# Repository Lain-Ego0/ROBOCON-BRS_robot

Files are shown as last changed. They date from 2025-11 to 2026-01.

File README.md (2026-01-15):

# ROBOCON-BRS_robot/黑岩射手
ROBOCON is a top-tier robotics competition that places high demands on mechanical reliability, electronic control stability, and visual accuracy.

ROBOCON作为机器人领域的顶尖赛事，对机械可靠性、电控稳定性、视觉准确性提出了较高的要求。

In the 2025 season, I was responsible for the full-stack R&D of the quadruped robot team, covering mechanical modeling, motion control, and autonomous navigation. Utilizing a carbon tube assembly mechanism similar to plant protection drones, force control algorithms, and 3D LiDAR mapping & navigation technology, our team achieved 30th place in the Speed Race, 31st in the Obstacle Race, and 34th in the Cross-Country Race at the 2025 ROBOCON (Jiangyin) among over 180 participating teams, winning Second Prize nationally in all three categories.

在2025赛季我基本完整负责了足式机器人一队从机械建模、运动控制到自主导航的全栈研发，采用类植保无人机碳管装配工艺机构+力控制算法+3D雷达建图导航技术，取得2025年ROBOCON（江阴）足式机器人竞速赛全国30名、障碍赛全国31名、越野赛全国34名（全国赛参赛队伍180余支）共三项国二的良好成绩。

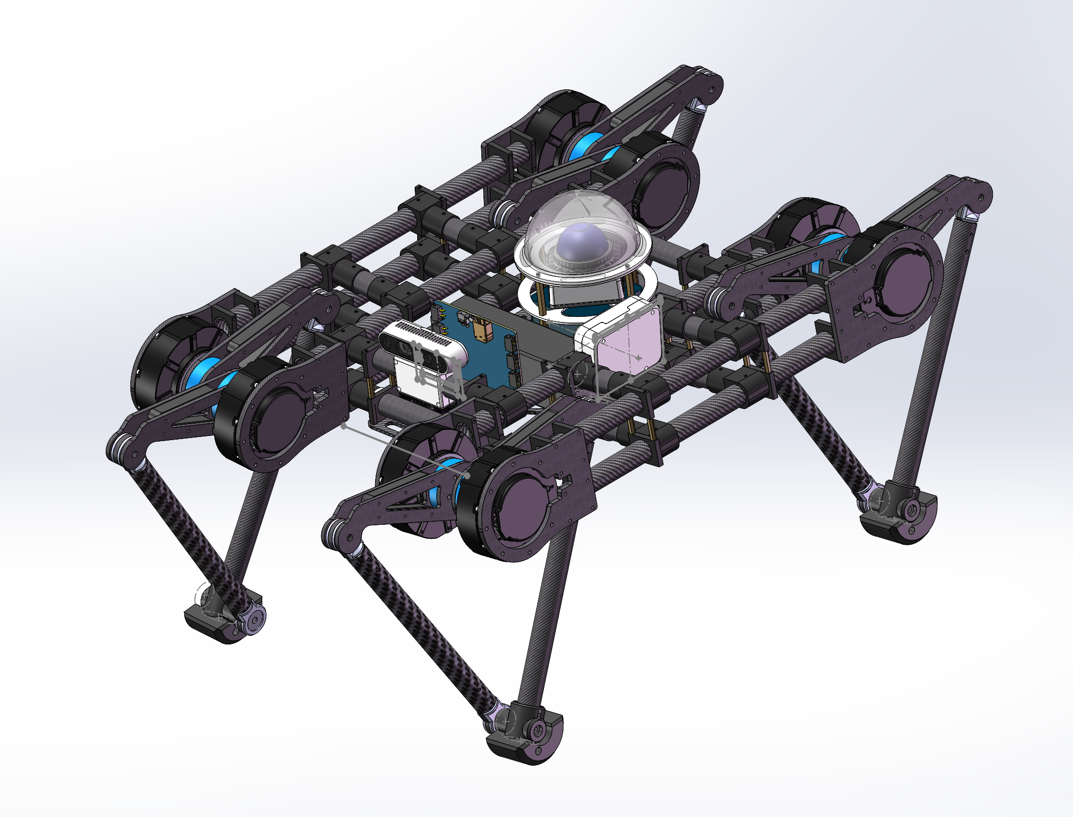
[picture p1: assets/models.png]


Post-calculation Visualization of Trajectory Demonstration and Inverse Kinematics Solution Demonstration in MATLAB

MATLAB计算后可视化的轨迹演示以及其逆解算演示

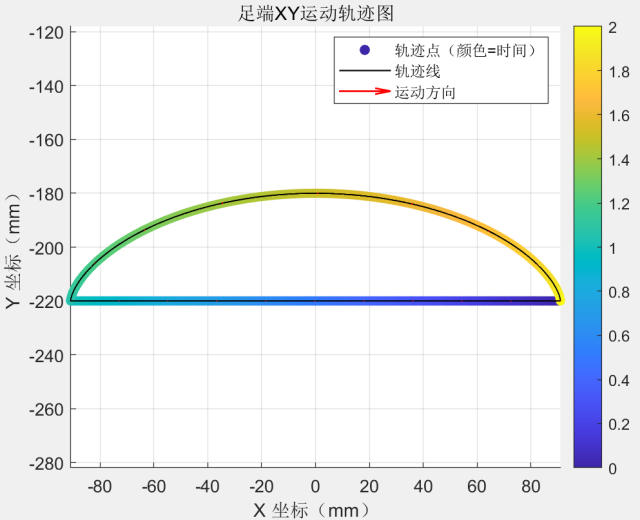
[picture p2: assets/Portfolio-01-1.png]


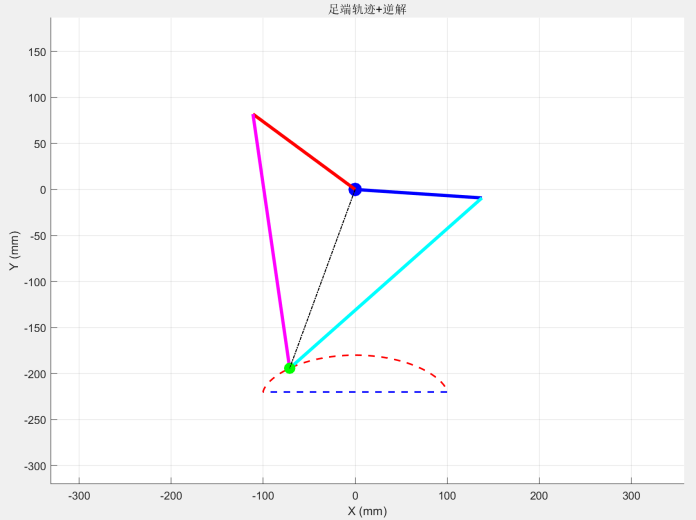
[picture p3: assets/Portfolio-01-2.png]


The system architecture diagram is shown in the figure.

系统架构图如图所示

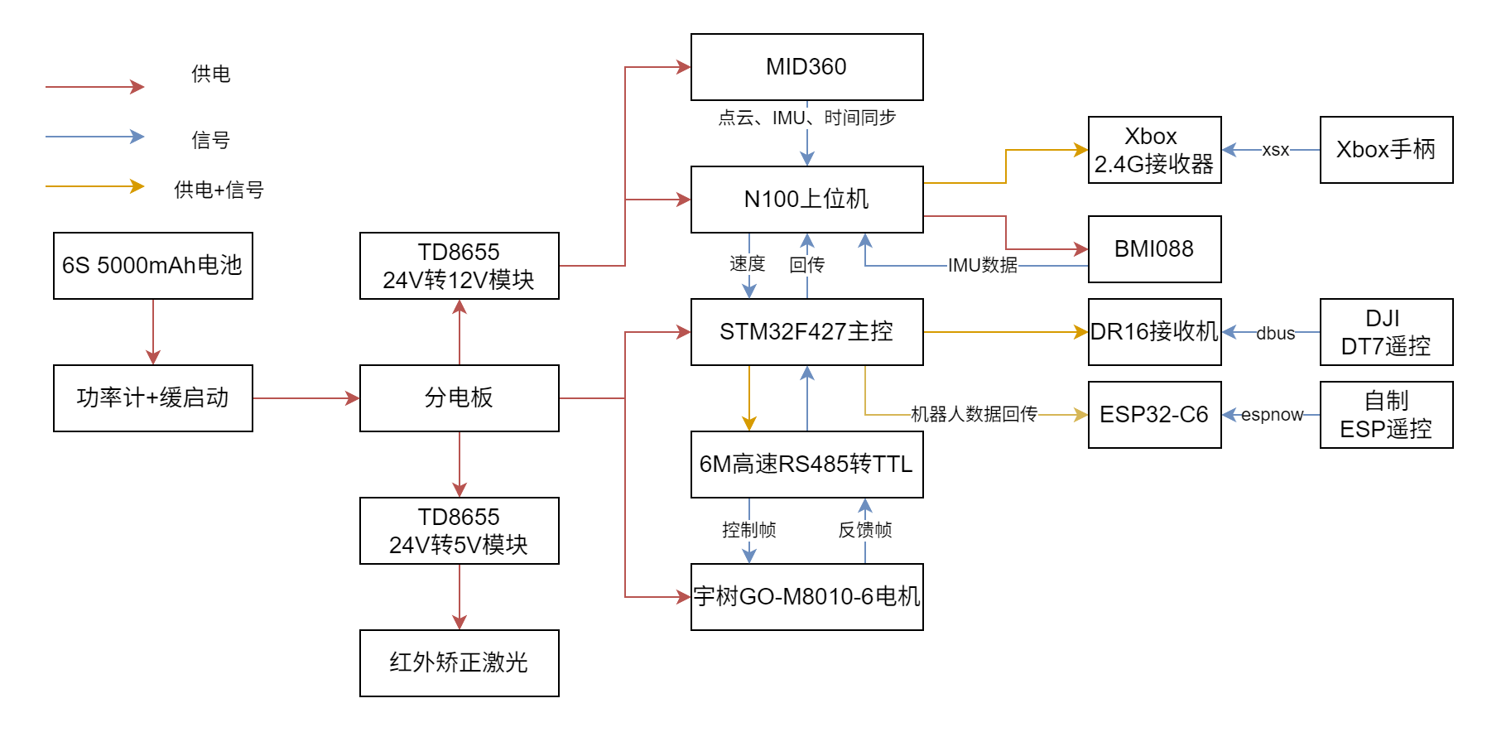
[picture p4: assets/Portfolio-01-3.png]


Data Reading Demonstration in Calibration Mode

校准模式的数据读取演示

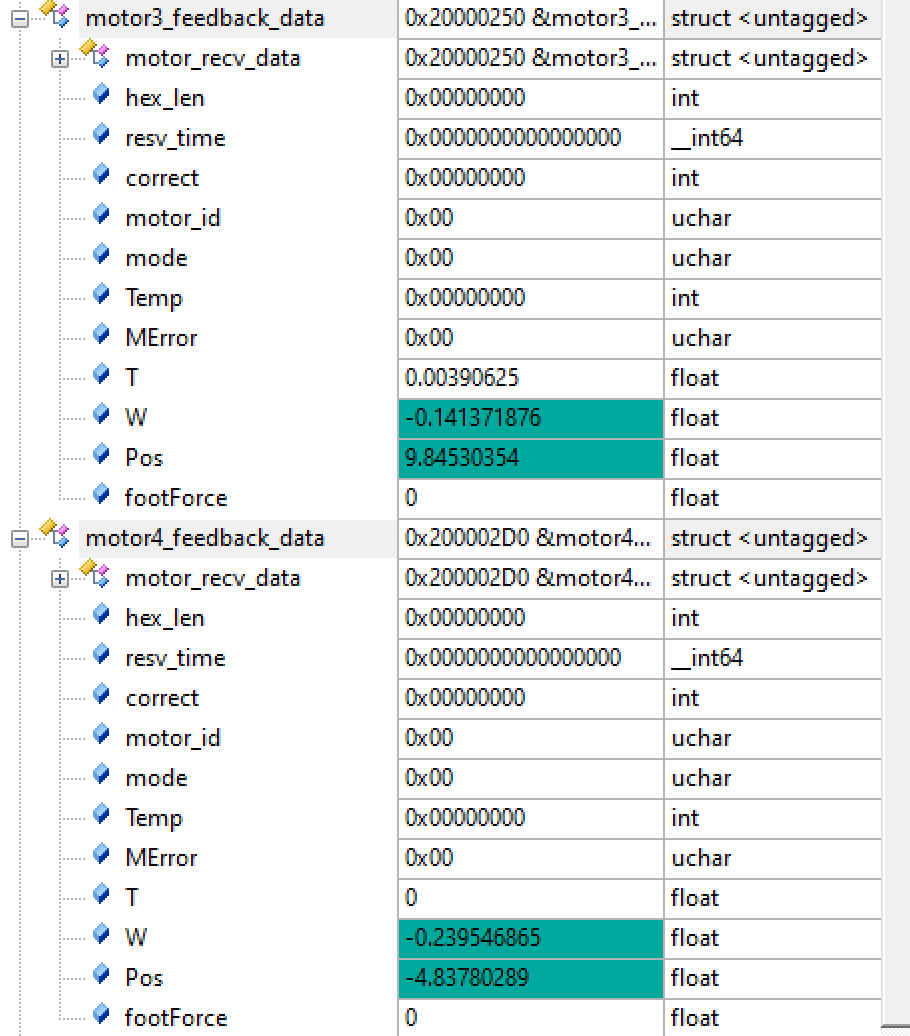
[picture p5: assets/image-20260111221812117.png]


# Project Timeline/项目时间线：

- August 2024: Project initiation

- December 2024: Completion of the first version of the mechanical prototype

- February 2025: Completion of the first version of the slave computer

- April 2025: Completion of the master computer

- June 2025: Completion of the navigation function

- July 2025: Completion of the second version of the slave computer; participation in the competition in the same month

- 2024年8月 项目启动 

- 2024年12月 完成第一版机械实物 

- 2025年2月 完成第一版下位机 

- 2025年4月 完成上位机 

- 2025年6月 完成导航功能 

- 2025年7月 完成第二版下位机 同月参赛。

# Update Log/更新记录：

- November 2025: Open-source mechanical structure
- December 2025: Open-source slave computer control software
- 2025年11月 开源机械结构
- 2025年12月 开源下位机控制软件
- ……

# Project Acknowledgements

Host computer

- https://github.com/66Lau/NEXTE_Sentry_Nav

- [使用mid360从0开始搭建实物机器人入门级导航系统，基于Fast_Lio,Move_Base](https://blog.csdn.net/weixin_52612260/article/details/134124028)
- [基于Mid360、FAST-LIO2（建图）与MOVE-BASE（导航）的串口发送方案](https://blog.csdn.net/Hbutneymar/article/details/147161479)

```mermaid
graph TD
    A[MID360激光雷达 发送点云数据] --> B[FAST_LIO2 三维激光建图]
    B --> C[三维点云PCD → 二维栅格地图 格式转换]
    C --> D[机器人全局重定位]
    D --> E[ROS发布机器人初始位置]
    E --> F[move_base导航框架 路径规划与导航]
    F --> G[发布导航目标点]
    G --> H[串口模块 订阅 /Odometry + /cmd_vel 话题数据]
```

Slave computer

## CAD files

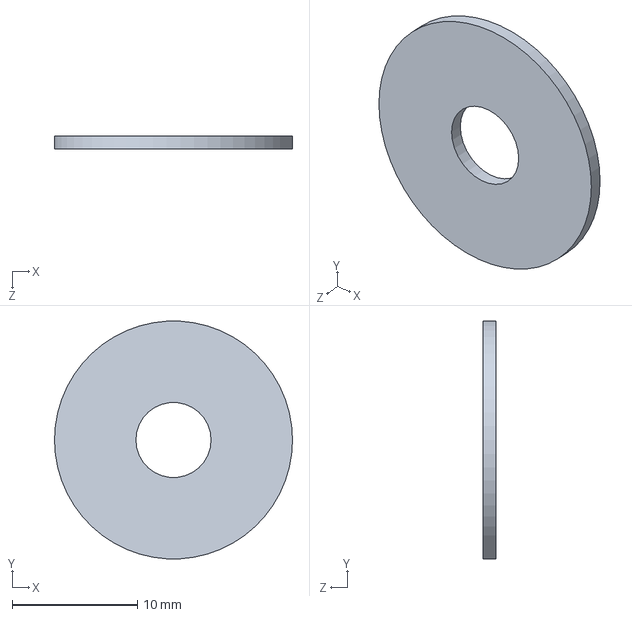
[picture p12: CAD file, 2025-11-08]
1.Hardware/models/平推滚子垫片.SLDPRT
19.0 x 19.0 x 1.00 mm

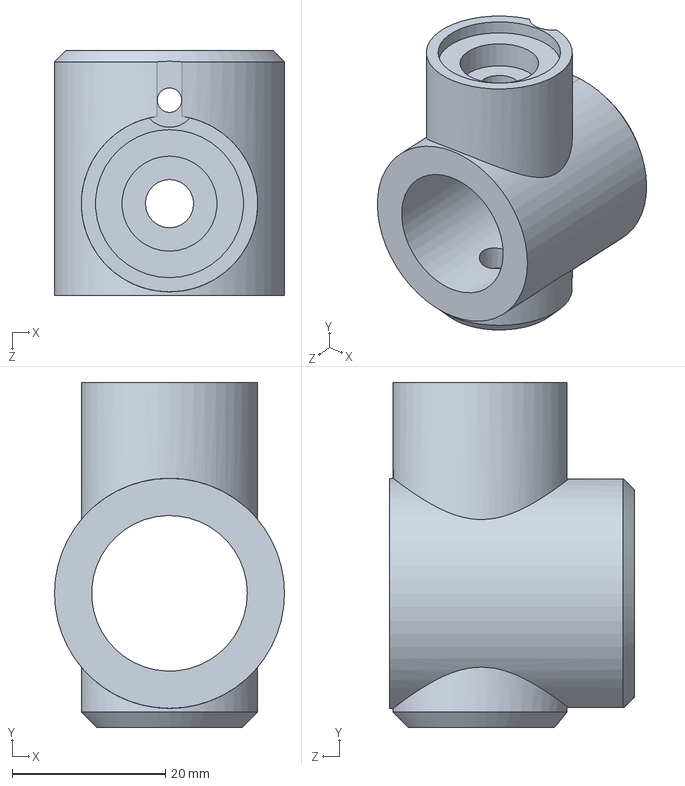
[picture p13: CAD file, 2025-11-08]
1.Hardware/models/打印件-小腿连接件3.0.SLDPRT
30.0 x 45.0 x 32.0 mm

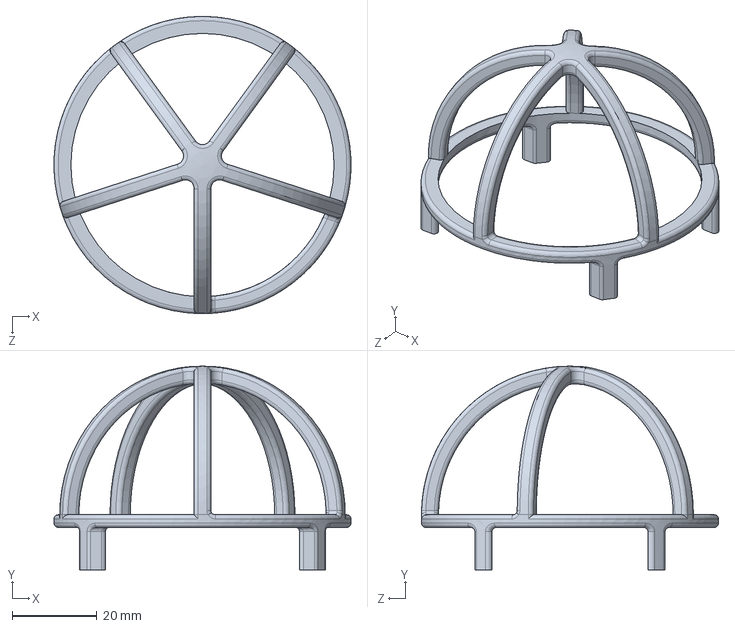
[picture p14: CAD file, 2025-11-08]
1.Hardware/models/雷达保护罩.SLDPRT
70.0 x 48.0 x 70.0 mm

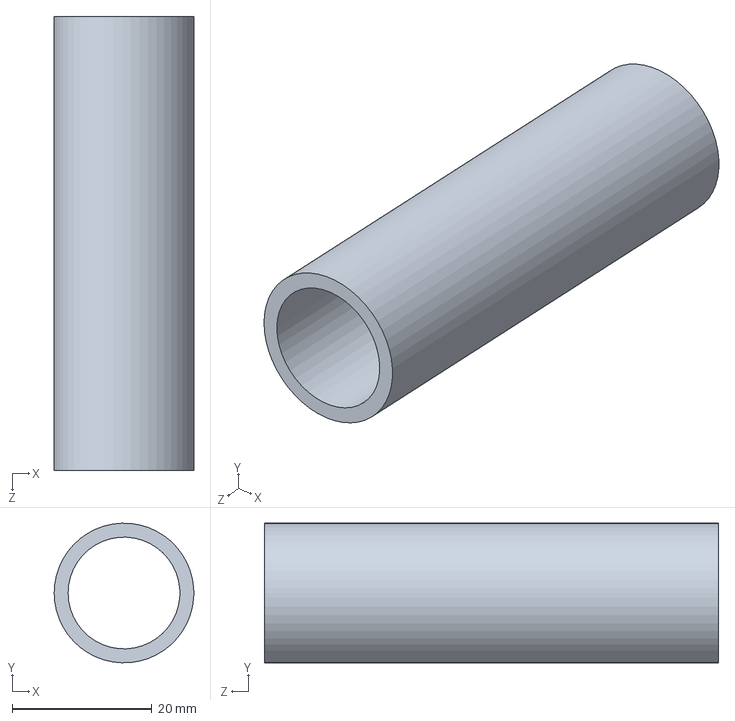
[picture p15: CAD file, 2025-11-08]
1.Hardware/models/碳纤管-狗身侧边S.SLDPRT
20.0 x 20.0 x 65.0 mm

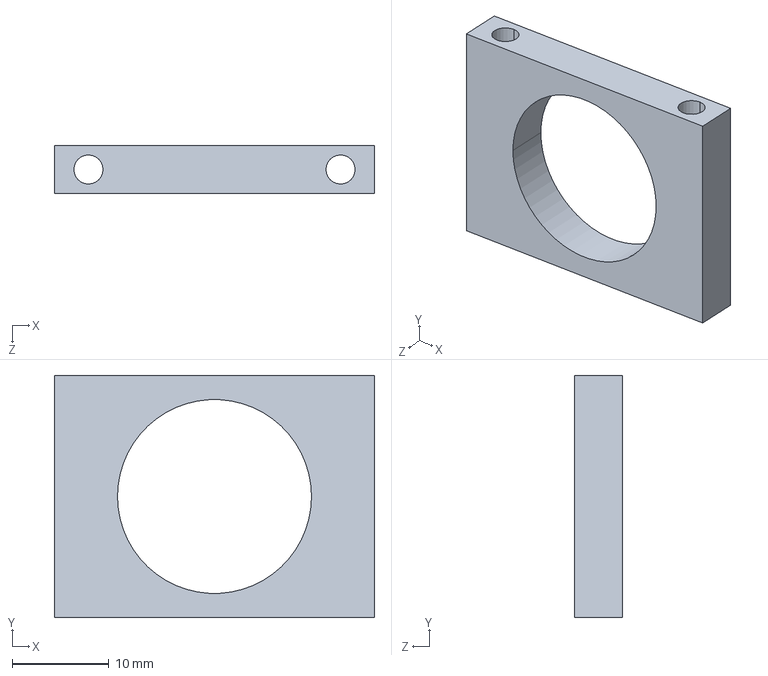
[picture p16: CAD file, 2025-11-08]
1.Hardware/models/铝合金-方型管夹.SLDPRT
33.0 x 25.0 x 5.00 mm

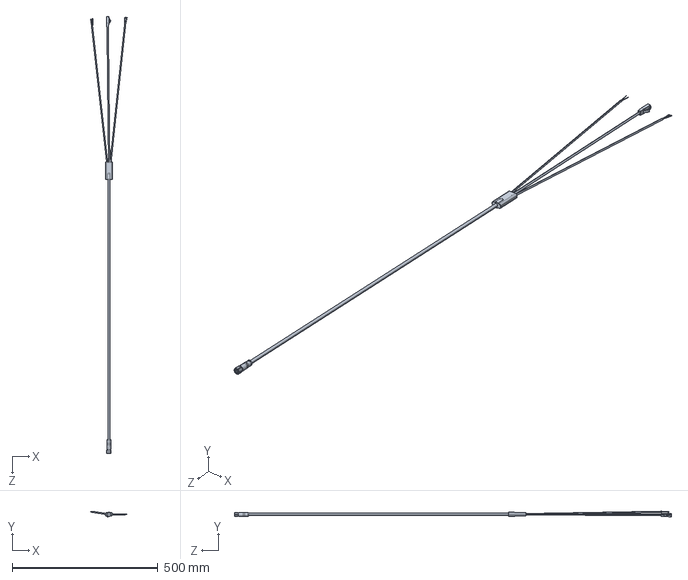
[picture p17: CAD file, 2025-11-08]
1.Hardware/models/Livox 航插一分三线.SLDPRT
126.1 x 19.0 x 1499.1 mm

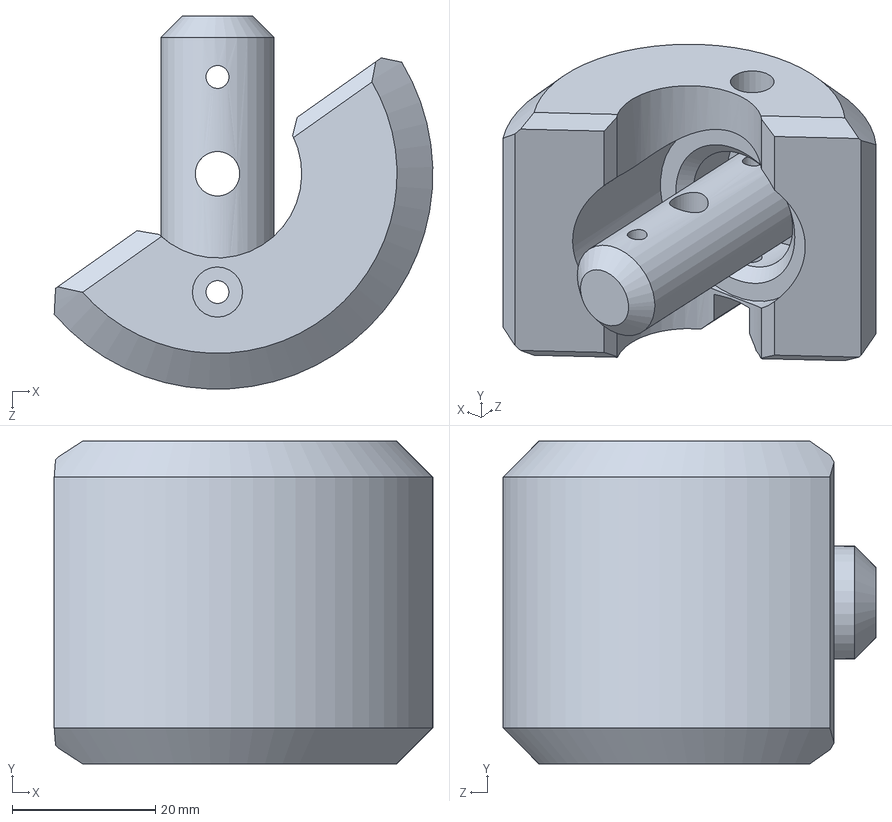
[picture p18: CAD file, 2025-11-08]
1.Hardware/models/打印件-足端4.0.SLDPRT
52.8 x 45.0 x 52.0 mm

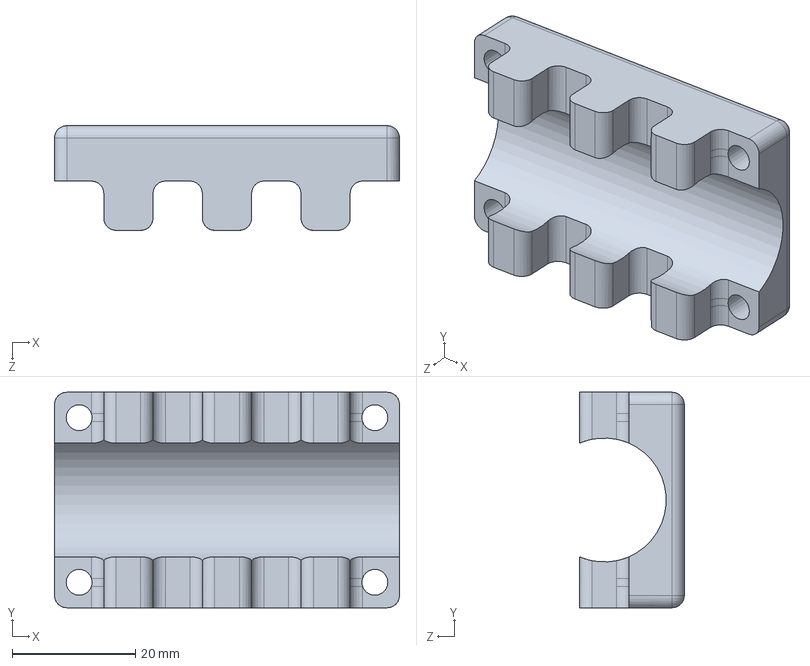
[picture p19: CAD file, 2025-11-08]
1.Hardware/models/急停定位打印件2.SLDPRT
56.0 x 35.0 x 17.0 mm

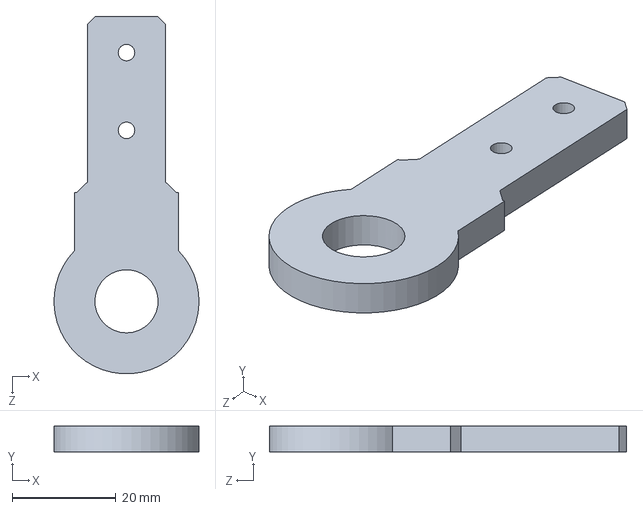
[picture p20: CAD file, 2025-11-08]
1.Hardware/models/打印件-大小腿连接件3.0-1.SLDPRT
28.0 x 5.00 x 69.0 mm

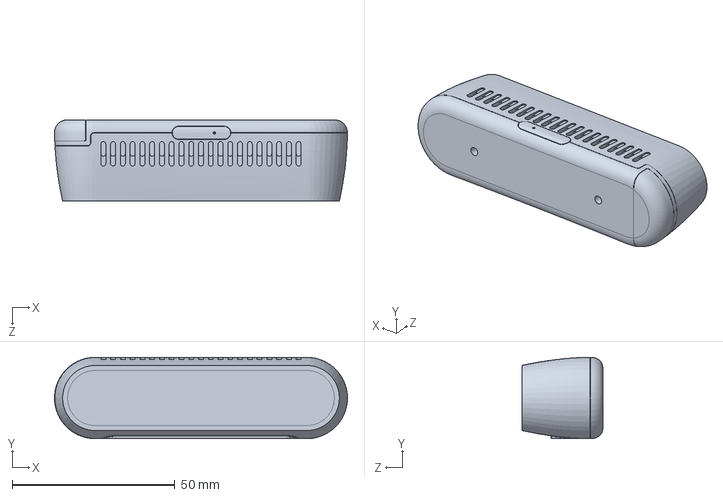
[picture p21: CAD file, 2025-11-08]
1.Hardware/models/IntelRealsense_D435_Multibody.SLDPRT
90.0 x 25.0 x 25.0 mm

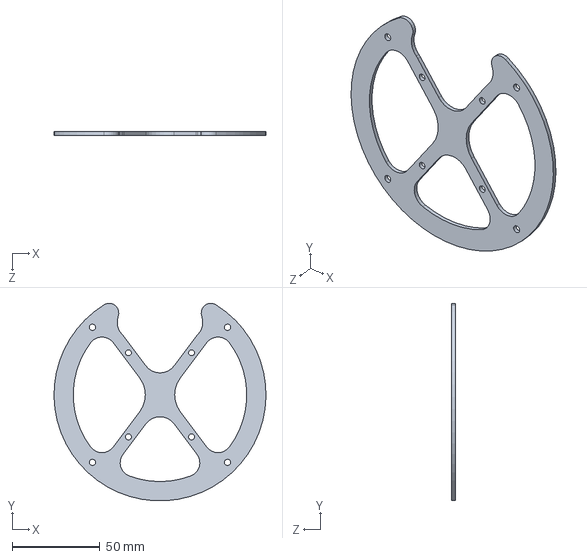
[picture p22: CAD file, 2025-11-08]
1.Hardware/models/玻纤-雷达保护罩2.SLDPRT
121.0 x 112.6 x 2.00 mm

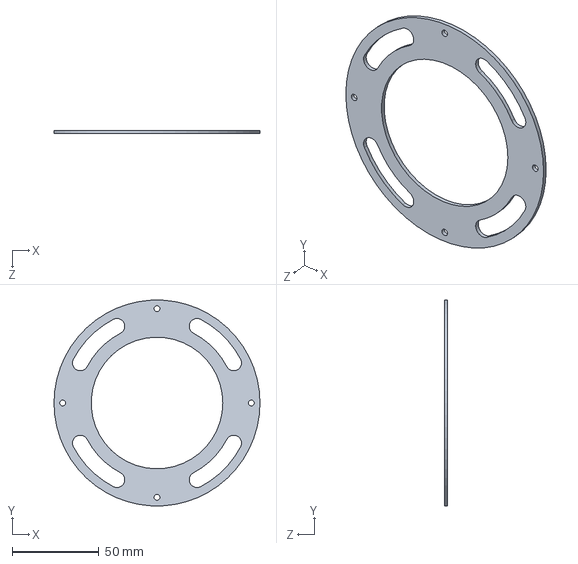
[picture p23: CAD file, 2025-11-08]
1.Hardware/models/玻纤-雷达保护罩1.SLDPRT
119.0 x 118.8 x 2.00 mm

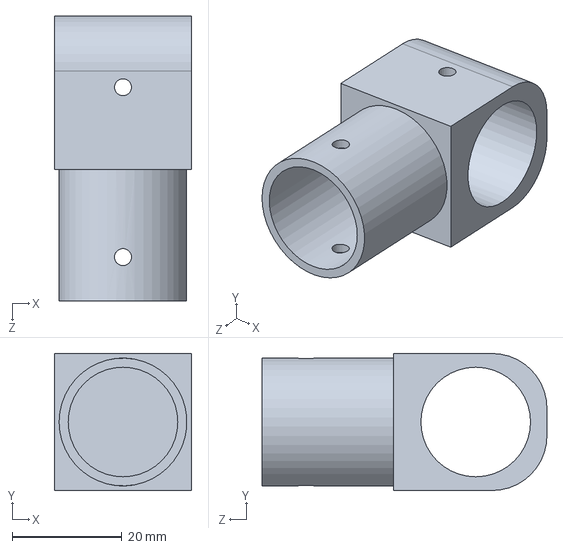
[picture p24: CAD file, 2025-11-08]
1.Hardware/models/铝合金-T型三通管夹.SLDPRT
25.0 x 25.0 x 52.0 mm

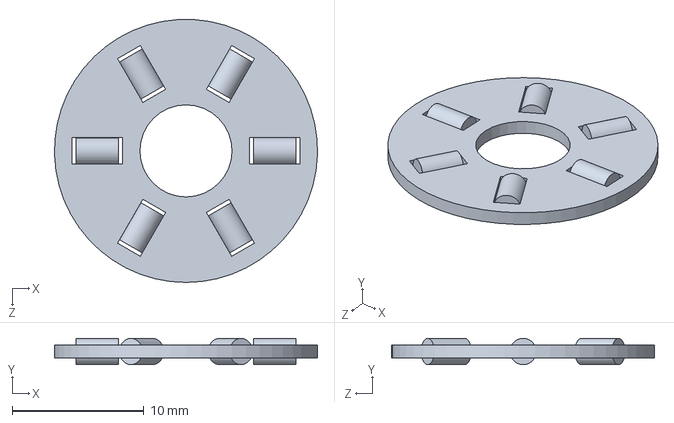
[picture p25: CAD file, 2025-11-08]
1.Hardware/models/GB╱T 4605-2003[推力滚针和保持架组件AXK0619].sldprt
20.0 x 2.00 x 20.0 mm

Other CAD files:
1.Hardware/models/分电板.SLDASM
1.Hardware/models/碳纤管-狗身横向（上）2.0S.SLDPRT
1.Hardware/models/碳纤管-狗身纵向.SLDPRT
1.Hardware/models/碳纤板-大腿3.0右.SLDPRT
1.Hardware/models/6-12-4轴承.SLDPRT
1.Hardware/models/m3 21 铜柱（侧边）2022.SLDPRT
1.Hardware/models/主控-M6S.SLDPRT
1.Hardware/models/开关定位打印件1.SLDPRT
1.Hardware/models/开关定位打印件2.SLDPRT
1.Hardware/models/急停定位打印件1.SLDPRT
1.Hardware/models/打印件-大小腿连接件3.0-2.SLDPRT
1.Hardware/models/打印件-大腿垫片.SLDPRT
1.Hardware/models/打印件-电机连接件（夹板内）3.0.SLDPRT
1.Hardware/models/玻纤-底版.SLDPRT
1.Hardware/models/玻纤-管固定件.SLDPRT
1.Hardware/models/电池.SLDPRT
1.Hardware/models/碳纤板-大腿3.0左 .SLDPRT
1.Hardware/models/碳纤板-电机固定板2.0S.SLDPRT
1.Hardware/models/碳纤管-小腿1.SLDPRT
1.Hardware/models/碳纤管-小腿2.SLDPRT
1.Hardware/models/碳纤管-狗身横向（下）2.0S.SLDPRT
1.Hardware/models/躯干垫片.SLDPRT
1.Hardware/models/铜柱 m4 35.SLDPRT
1.Hardware/models/铜柱 m4 50.SLDPRT
1.Hardware/models/雷达保护罩2.SLDPRT

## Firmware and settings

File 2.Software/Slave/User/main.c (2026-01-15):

#include "main.h"

volatile uint8_t g_system_tick = 0;

/* 全局变量 */
MOTOR_send motor_control_clear; 
uint8_t Motor_Rxflag = 0;
uint8_t Motor_Rx_date = 0;

volatile int RC_RX_flag = 0;

int rc_watchdog_count = 0;
#define RC_TIMEOUT_MAX 500 // 500ms 超时

// 时间与步态参数
int tim_t = 0; // 启动延时
int time_currently = 0;
int time_turn = 0;
int step_rate = 250; 

extern uint8_t RC[18];
extern int Dog_Iinit;
extern int step_turn_flag;

// 发送索引
int motor_send_index = 0; 

// 足端轨迹坐标
float foot_track_x1 = 0.0f, foot_track_y1 = 0.0f;
float foot_track_x2 = 0.0f, foot_track_y2 = 0.0f;
float foot_track_x3 = 0.0f, foot_track_y3 = 0.0f;
float foot_track_x4 = 0.0f, foot_track_y4 = 0.0f;	

int main(void)
{
    // 1. 硬件外设初始化
	RC_USART1_Config();				
	HOST_USART_Config();			
	MOTOR_CONTROL1_USART_Config();	
	
	USART1_DMA_Config();			
	USART6_DMA_Config();			
	
	RC_DMA_NVIC_Configuration();		
	Motor_DMA_NVIC_Configuration();	
	
	USART_DMACmd(USART1, USART_DMAReq_Rx, ENABLE);	
	USART_DMACmd(USART6, USART_DMAReq_Rx, ENABLE);	
	
	HSE_SetSysClock(12, 336, 2, 7); 

    // 2. 算法模块初始化
	PID_Init();						
	Motor_Mode_Init();				

    // 3. 启动定时器 
	TIMx_Configuration(); 
	
	// 4.上电保护
	while(tim_t < 2000) { 
        if(g_system_tick) { 
            tim_t++; 
            g_system_tick = 0; 
        }
    }
	memset(&rc_rc, 0, sizeof(rc_rc));
    rc_rc.s1 = 2; // 系统模式
    rc_rc.s2 = 3; // 趴下状态
	
	while(1)
	{	
        if (g_system_tick)
        {
            g_system_tick = 0; // 清除标志

            // --- 1. 数据处理 ---
			if (RC_RX_flag == 1) {
                RC_RX_flag = 0;
                rc_rc_date(); // 解析数据
                rc_watchdog_count = 0; // 喂狗
            } else {
                rc_watchdog_count++;
            }
			
			if (rc_watchdog_count > RC_TIMEOUT_MAX) {
                // 遥控器超时强制进入安全模式
                rc_rc.ch0 = 0; rc_rc.ch1 = 0; rc_rc.ch2 = 0; rc_rc.ch3 = 0;
                rc_rc.s1 = 2; 
                rc_rc.s2 = 3; 
                if(rc_watchdog_count > 10000) rc_watchdog_count = 10000; 
            }

            // --- 2. 步态轨迹规划 ---
            foot_track(&foot_track_x1, &foot_track_y1, step_rate, time_currently, 200, time_turn, 2, 1);           
            foot_track(&foot_track_x2, &foot_track_y2, step_rate, time_currently, 200, time_turn, 1, 3);         
            foot_track(&foot_track_x3, &foot_track_y3, step_rate, time_currently, 200, time_turn, 2, 2);          
            foot_track(&foot_track_x4, &foot_track_y4, step_rate, time_currently, 200, time_turn, 1, 4);

            // --- 3. 运动逆解 ---
            counter_motion(foot_track_x1, foot_track_y1, &Leg_Motors[0].target_angle, &Leg_Motors[1].target_angle);
            counter_motion(foot_track_x2, foot_track_y2, &Leg_Motors[3].target_angle, &Leg_Motors[2].target_angle);
            counter_motion(foot_track_x3, foot_track_y3, &Leg_Motors[4].target_angle, &Leg_Motors[5].target_angle);
            counter_motion(foot_track_x4, foot_track_y4, &Leg_Motors[7].target_angle, &Leg_Motors[6].target_angle);

            // --- 4. 控制 ---
            Motor_pid_compute_all();	//PID输出		           
            Motor_data_update_all();	//更新数据帧
            
            // --- 5. 通信发送 --- 大约使用0.8ms，也可以修改运行时间
            for(int k=0; k<8; k++) {
                Motor_date_send_sequential(&motor_send_index);
            }
            
            motor_send_index = 0; // 复位索引确保同步
        }
	}
}

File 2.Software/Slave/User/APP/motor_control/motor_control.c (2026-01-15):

#include "motor_control.h" 
#include "pid.h"
#include "GO_M8010_6.h"
#include "bsp_debug_usart.h"
#include "bsp_key.h" 
#include "remote.h" 
#include "math.h"
#include <stdlib.h> 

/* -------------------------------------------------------------------------
   1.配置参数
   ------------------------------------------------------------------------- */
#define SPEED_P 0.01f
#define SPEED_I 0.0006f
#define SPEED_D 0.0015f    
#define RANG_P  35.9f
#define RANG_I  0.0f
#define RANG_D  1.0f
#define SPEED_MAX_OUT  3.50f
#define SPEED_MAX_IOUT 0.2f
#define RANG_MAX_OUT   10000.0f
#define RANG_MAX_IOUT  0.2f

#define LEG_L1 138.0f       
#define LEG_L2 279.0f       
#define LEG_MAX_LEN 400.0f  
#define LEG_MIN_LEN 50.0f   
#define REDUCTION_RATIO 6.33f
#define PI 3.1415926f

Motor_Unit_TypeDef Leg_Motors[8];
MOTOR_recv motor_feedback_data; 
extern MOTOR_send motor_control_clear; 

// 校准模式标志 (1=开启, 0=关闭)
int g_calibration_mode = 0;

// 外部引用
extern int step_rate; 
int step_cycle = 500; 
extern int step_turn_flag;

// 状态变量
float g_stand_progress = 0.0f; // 0.0(趴下) -> 1.0(站立)
int Dog_Iinit = 0; 

// ========================================================
// 跳跃变量实体定义
// ========================================================
int dog_jump_time = 0;
int dog_jump_flag = 0;
int dog_jump_time_2 = 0;
int dog_jump_flag_2 = 0;
int dog_jump_time_3 = 0;
int dog_jump_flag_3 = 0;

const fp32 Speed_PID_Params[3] = {SPEED_P, SPEED_I, SPEED_D};	
const fp32 Rang_PID_Params[3]  = {RANG_P,  RANG_I,  RANG_D};		

const float Motor_Offsets[8] = {
    8.652f, -9.970f, 4.984f, -13.648f, 4.397f, -17.293f, 11.656f, -8.065f
};
const float Motor_Directions[8] = {
    1.0f, 1.0f, -1.0f, -1.0f, -1.0f, -1.0f, 1.0f, 1.0f
};

// 步态配置
typedef struct {
    float leg_high;
    float leg_lift_height;
    float start_point;
    float step_length;
    float start_point_turn;
    float step_length_turn;
    int   local_step_rate;
} GaitConfig_t;

static GaitConfig_t g_gait;

/* -------------------------------------------------------------------------
   2.初始化与 PID 函数
   ------------------------------------------------------------------------- */

void PID_Init(void) {
    for(int i = 0; i < 8; i++) {
        PID_init(&Leg_Motors[i].speed_pid, PID_POSITION, Speed_PID_Params, SPEED_MAX_OUT, SPEED_MAX_IOUT);
        PID_init(&Leg_Motors[i].angle_pid, PID_POSITION, Rang_PID_Params,  RANG_MAX_OUT,  RANG_MAX_IOUT);
    }
}

void Motor_Mode_Init(void) {
    motor_control_clear.id = 15; motor_control_clear.mode = 1; modify_data(&motor_control_clear);
    for(int i = 0; i < 8; i++) {
        Leg_Motors[i].id = i + 2;
        Leg_Motors[i].offset = Motor_Offsets[i];
        Leg_Motors[i].dir_sign = Motor_Directions[i];
        Leg_Motors[i].control.id = Leg_Motors[i].id;
        Leg_Motors[i].control.mode = 1;
		
		// 初始化目标角度为当前角度，防止上电瞬间转动
        Leg_Motors[i].target_angle = 0.0f;
		
        modify_data(&Leg_Motors[i].control);
    }
}

// 校准模式
void Motor_pid_compute_all(void) {
    for(int i = 0; i < 8; i++) {
        // 如果处于校准模式，强制输出力矩为0，方便手动掰腿
        if (g_calibration_mode == 1) {
            Leg_Motors[i].control.T = 0.0f;
            // 清除PID积分项，防止退出校准时突变
            Leg_Motors[i].speed_pid.Iout = 0;
            Leg_Motors[i].angle_pid.Iout = 0;
            continue; 
        }

        float real_pos = Leg_Motors[i].feedback.Pos + Leg_Motors[i].offset;
        float target = Leg_Motors[i].target_angle * Leg_Motors[i].dir_sign;
        float speed_target = PID_calc(&Leg_Motors[i].angle_pid, real_pos, target);
        Leg_Motors[i].control.T = PID_calc(&Leg_Motors[i].speed_pid, Leg_Motors[i].feedback.W, speed_target);
    }
}

void Motor_data_update_all(void) {
    for(int i = 0; i < 8; i++) modify_data(&Leg_Motors[i].control);
}

int Motor_date_send_sequential(int *current_index) {
    if (*current_index < 0 || *current_index > 7) *current_index = 0;
    Usart_SendStr_length(USART6, ((uint8_t *)(&Leg_Motors[*current_index].control)), Leg_Motors[*current_index].control.hex_len);
    (*current_index)++;
    if (*current_index > 7) *current_index = 0;
    return 0;
}

void counter_motion(float X, float Y, float *range1, float *range2) {
    float L_sq = X * X + Y * Y;
    float L = sqrtf(L_sq);
    if (L > LEG_MAX_LEN) L = LEG_MAX_LEN;
    if (L < LEG_MIN_LEN) L = LEG_MIN_LEN;

    float sin_arg = X / L;
    if (sin_arg > 1.0f) sin_arg = 1.0f; 
    if (sin_arg < -1.0f) sin_arg = -1.0f;
    float range_Leg = asinf(sin_arg);

    float cos_arg = (L * L + LEG_L1 * LEG_L1 - LEG_L2 * LEG_L2) / (2.0f * LEG_L1 * L);
    if (cos_arg > 1.0f) cos_arg = 1.0f; 
    if (cos_arg < -1.0f) cos_arg = -1.0f;
    float range_separate = acosf(cos_arg);
	
    *range1 = (PI - (range_separate - range_Leg)) * REDUCTION_RATIO;
    *range2 = (PI - (range_separate + range_Leg)) * REDUCTION_RATIO;
}

/* -------------------------------------------------------------------------
   3.状态处理逻辑
   ------------------------------------------------------------------------- */

static inline float Get_Cycloid(float start, float end, float t) {
    float len = start - end;
    return start - len * (t - 0.15915f * sinf(2.0f * PI * t));
}
static inline float Get_Height_Sine(float base, float lift, float t) {
    return base - lift * (0.5f - 0.5f * cosf(2.0f * PI * t));
}

// 步态参数更新
static void Update_Gait_Params(void) {
    // 默认
    g_gait.leg_high = 205.0f;
    g_gait.leg_lift_height = 50.0f;
    g_gait.start_point = 75.0f;
    g_gait.start_point_turn = 70.0f;
    g_gait.local_step_rate = 250;

    if (rc_rc.s1 == 3) { // 运动模式
        if (rc_rc.s2 == 1) { // 快速
            g_gait.local_step_rate = 175;
            g_gait.leg_high = 210; 
            g_gait.leg_lift_height = 40;
        } else if (rc_rc.s2 == 2) { // 慢速
            g_gait.local_step_rate = 300;
             g_gait.leg_high = 220;
        } else { // 中速 (S2==3)
            g_gait.local_step_rate = 220;
            g_gait.leg_high = 215;
        }
    }

    g_gait.step_length = g_gait.start_point * 2.0f;
    g_gait.step_length_turn = g_gait.start_point_turn * 2.0f;
    
    if (g_gait.local_step_rate == 0) g_gait.local_step_rate = 250;
    step_rate = g_gait.local_step_rate;
    step_cycle = step_rate * 2;
}

// 系统模式处理
static void Handle_System(float *X, float *Y, int cmd_type, int dir_mode) {
    const float SPEED_FACTOR = 0.001f; // 升降速度

    // S2=1: 启动 (0 -> 1)
    if (cmd_type == 1) {
        g_stand_progress += SPEED_FACTOR;
        if (g_stand_progress > 1.0f) g_stand_progress = 1.0f;
    }
    // S2=3: 趴下 (1 -> 0)
    else if (cmd_type == 3) {
        g_stand_progress -= SPEED_FACTOR;
        if (g_stand_progress < 0.0f) g_stand_progress = 0.0f;
    }
    
    // 更新旧的显示变量
    Dog_Iinit = (int)(g_stand_progress * 2000);

    float init_x_offset = (dir_mode == 1 || dir_mode == 3) ? 160.0f : -160.0f;
    *X = init_x_offset * (1.0f - g_stand_progress);
    *Y = 40.0f + (g_gait.leg_high - 40.0f) * g_stand_progress;
}
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

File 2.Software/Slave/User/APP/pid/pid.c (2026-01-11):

/**
  ****************************(C) COPYRIGHT 2019 DJI****************************
  * @file       pid.c/h
  * @brief      pid实现函数，包括初始化，PID计算函数，
  * @note       
  * @history
  *  Version    Date            Author          Modification
  *  V1.0.0     Dec-26-2018     RM              1. 完成
  *
  @verbatim
  ==============================================================================

  ==============================================================================
  @endverbatim
  ****************************(C) COPYRIGHT 2019 DJI****************************
  */

#include "pid.h"

//pid结构体初始化
pid_type_def Motor2_speed_PID;
pid_type_def Motor2_rang_PID;
pid_type_def Motor3_speed_PID;
pid_type_def Motor3_rang_PID;
pid_type_def Motor4_speed_PID;
pid_type_def Motor4_rang_PID;
pid_type_def Motor5_speed_PID;
pid_type_def Motor5_rang_PID;
pid_type_def Motor6_speed_PID;
pid_type_def Motor6_rang_PID;
pid_type_def Motor7_speed_PID;
pid_type_def Motor7_rang_PID;
pid_type_def Motor8_speed_PID;
pid_type_def Motor8_rang_PID;
pid_type_def Motor9_speed_PID;
pid_type_def Motor9_rang_PID;

#define LimitMax(input, max)   \
    {                          \
        if (input > max)       \
        {                      \
            input = max;       \
        }                      \
        else if (input < -max) \
        {                      \
            input = -max;      \
        }                      \
    }

/**
  * @brief          pid struct data init
  * @param[out]     pid: PID结构数据指针
  * @param[in]      mode: PID_POSITION:普通PID
  *                 PID_DELTA: 差分PID
  * @param[in]      PID: 0: kp, 1: ki, 2:kd
  * @param[in]      max_out: pid最大输出
  * @param[in]      max_iout: pid最大积分输出
  * @retval         none
  */
void PID_init(pid_type_def *pid, uint8_t mode, const fp32 PID[3], fp32 max_out, fp32 max_iout)
{
    if (pid == 0 || PID == 0)
    {
        return;
    }
    pid->mode = mode;
    pid->Kp = PID[0];
    pid->Ki = PID[1];
    pid->Kd = PID[2];
    pid->max_out = max_out;
    pid->max_iout = max_iout;
    pid->Dbuf[0] = pid->Dbuf[1] = pid->Dbuf[2] = 0.0f;
    pid->error[0] = pid->error[1] = pid->error[2] = pid->Pout = pid->Iout = pid->Dout = pid->out = 0.0f;
}

/**
  * @brief          pid计算
  * @param[out]     pid: PID结构数据指针
  * @param[in]      ref: 反馈数据
  * @param[in]      set: 设定值
  * @retval         pid输出
  */
fp32 PID_calc(pid_type_def *pid, fp32 ref, fp32 set)
{
    if (pid == 0)
    {
        return 0.0f;
    }

    pid->error[2] = pid->error[1];
    pid->error[1] = pid->error[0];
    pid->set = set;
    pid->fdb = ref;
    pid->error[0] = set - ref;
    if (pid->mode == PID_POSITION)
    {
        pid->Pout = pid->Kp * pid->error[0];
        pid->Iout += pid->Ki * pid->error[0];
        pid->Dbuf[2] = pid->Dbuf[1];
        pid->Dbuf[1] = pid->Dbuf[0];
        pid->Dbuf[0] = (pid->error[0] - pid->error[1]);
        pid->Dout = pid->Kd * pid->Dbuf[0];
        LimitMax(pid->Iout, pid->max_iout);
        pid->out = pid->Pout + pid->Iout + pid->Dout;
        LimitMax(pid->out, pid->max_out);
    }
    else if (pid->mode == PID_DELTA)
    {
        pid->Pout = pid->Kp * (pid->error[0] - pid->error[1]);
        pid->Iout = pid->Ki * pid->error[0];
        pid->Dbuf[2] = pid->Dbuf[1];
        pid->Dbuf[1] = pid->Dbuf[0];
        pid->Dbuf[0] = (pid->error[0] - 2.0f * pid->error[1] + pid->error[2]);
        pid->Dout = pid->Kd * pid->Dbuf[0];
        pid->out += pid->Pout + pid->Iout + pid->Dout;
        LimitMax(pid->out, pid->max_out);
    }
    return pid->out;
}

fp32 PID_calc_rang(pid_type_def *pid, fp32 ref, fp32 set)
{
    if (pid == 0)
    {
        return 0.0f;
    }

    pid->error[2] = pid->error[1];
    pid->error[1] = pid->error[0];
    pid->set = set;
    pid->fdb = ref;
    pid->error[0] = set - ref;
    if (pid->mode == PID_POSITION)
    {
        pid->Pout = pid->Kp * pid->error[0];
        pid->Iout += pid->Ki * pid->error[0];
        pid->Dbuf[2] = pid->Dbuf[1];
        pid->Dbuf[1] = pid->Dbuf[0];
        pid->Dbuf[0] = (pid->error[0] - pid->error[1]);
        pid->Dout = pid->Kd * pid->Dbuf[0];
        LimitMax(pid->Iout, pid->max_iout);
        pid->out = pid->Pout + pid->Iout + pid->Dout;
        LimitMax(pid->out, pid->max_out);
    }
    else if (pid->mode == PID_DELTA)
    {
        pid->Pout = pid->Kp * (pid->error[0] - pid->error[1]);
        pid->Iout = pid->Ki * pid->error[0];
        pid->Dbuf[2] = pid->Dbuf[1];
        pid->Dbuf[1] = pid->Dbuf[0];
        pid->Dbuf[0] = (pid->error[0] - 2.0f * pid->error[1] + pid->error[2]);
        pid->Dout = pid->Kd * pid->Dbuf[0];
        pid->out += pid->Pout + pid->Iout + pid->Dout;
        LimitMax(pid->out, pid->max_out);
    }
    return pid->out;
}

/**
  * @brief          pid out clear
  * @param[out]     pid: PID struct data point
  * @retval         none
  */
/**
  * @brief          pid 输出清除
  * @param[out]     pid: PID结构数据指针
  * @retval         none
  */
void PID_clear(pid_type_def *pid)
{
    if (pid == 0)
    {
        return;
    }

    pid->error[0] = pid->error[1] = pid->error[2] = 0.0f;
    pid->Dbuf[0] = pid->Dbuf[1] = pid->Dbuf[2] = 0.0f;
    pid->out = pid->Pout = pid->Iout = pid->Dout = 0.0f;
    pid->fdb = pid->set = 0.0f;
}

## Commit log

2025-11-08 Add hardware project and CAD model files
    Added new hardware project files (.epro) and a large set of SolidWorks part and assembly files (.SLDPRT, .SLDASM) under the 1.Hardware directory. These files likely represent new hardware designs and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
    [6-12-4轴承.SLDPRT, GB╱T 4605-2003[推力滚针和保持架组件AXK0619].sldprt, IntelRealsense_D435_Multibody.SLDPRT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]
2026-01-14 Migrate project to BRS-260114-0114-V2.1.2 version
    Removed old BRS-260111-2314-V2.1.2 source files and added or renamed all relevant files to the new BRS-260114-0114-V2.1.2 directory. This includes application, BSP, and library files, as well as main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
